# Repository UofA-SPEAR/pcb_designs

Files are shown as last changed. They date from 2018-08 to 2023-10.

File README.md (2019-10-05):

# SPEAR PCB Designs #

Central repository to hold PCB designs for SPEAR.

All board documentation shall be held in the [Wiki.](https://github.com/UofA-SPEAR/pcb_designs/wiki/).

## Onboarding

If you plan on contributing to the PCB designs, first, you need to go through this list:

1. Sign up for github, and fill out the new member form (contact the current team lead for this).
2. Follow the [GitHub Guides](https://guides.github.com/), specifically:
  - "Hello World"
  - "Understanding the GitHub flow."
  - "Documenting your projects on GitHub"
3. Follow the [Onboarding Task](https://github.com/UofA-SPEAR/pcb_designs/wiki/Onboarding-Task).

## Contributing

In order to start a new project, there are a few steps.

1. Create a new branch for your project.
2. Create a folder for your project, with the name of your project.
3. Create an Eagle library for your project.
4. Begin a documentation page on the wiki.

### Branches

Branches are a useful concept in Git, where you can work on your portion
of the project seperately from everyone else, and then "merge" your changes back in.

We make use of branches extensively. For every project, or new task, make a new branch, with
the naming scheme `project-name-yourname`, where "yourname" is ideally your first name, or at least
something that uniquely identifies you.

When you are finished your design, make a pull request to master, and assign the team
lead to review it. This is where the team lead will do a design review and ask to make
any required changes. Once these changes are made (or there are no changes), this code will be pulled into
the main repository, and the branch will be deleted.

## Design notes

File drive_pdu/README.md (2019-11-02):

# Drive System PDU #

## Overview ##

This is going to be a collaborative project, used as an EAGLE tutorial.

Features it needs to have:
- 4 Pairs of Anderson PP45 connectors
- 2 high power connectors for motor drivers
- 3v3 500mA + AMPMODU connectors for indicator board.
- Fuses

## Parts selection ##

- PP45 Parts:
	- Mouser #879-1345
	- Mouser #879-1345G6
	- Mouser #879-1336G1
- High power headers
	- TBD
- 3v3 regulator
	- TBD
- AMPMODU MTE connectors
	- DigiKey #A33893-ND
- Fuses/fuseholders
	- DigiKey #F5028-ND
	- DigiKey #486-3045-ND

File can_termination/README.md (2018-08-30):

# CAN Termination Board #

This is just a small board, designed to go on every electrical 'box' that has some options for CAN passthrough and termination to allow for a more "plug-and-play" approach to CAN bus.

It simply has two pass-through connections (so you can keep internal wiring consistent) and two termination connections (so you can hook boxes up in isolation without really worrying about which boards have termination resistors.

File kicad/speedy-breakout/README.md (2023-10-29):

# Speedy Breakout
This is a basic breakout board for our Speedy Microcontroller.
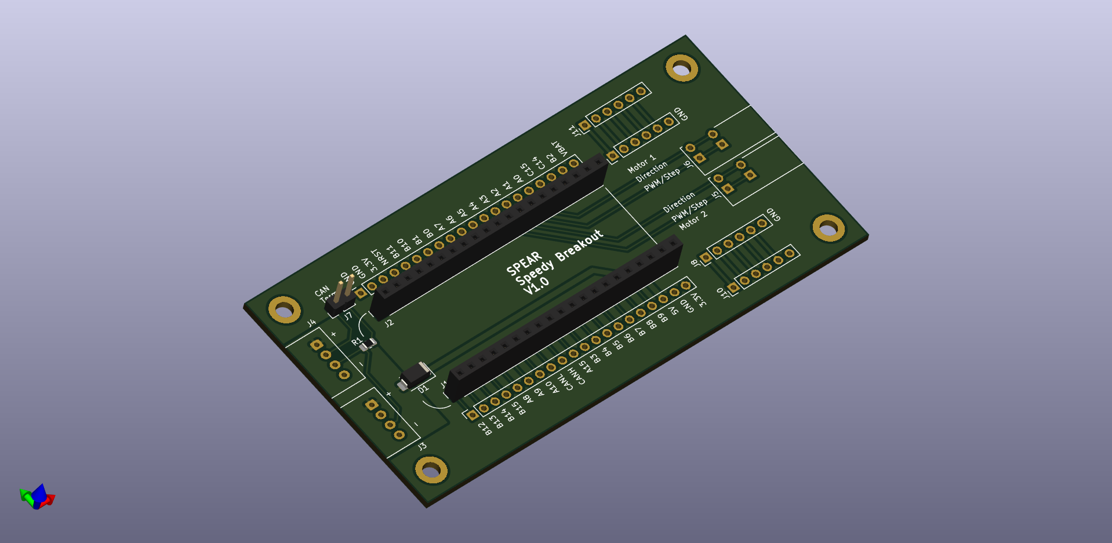
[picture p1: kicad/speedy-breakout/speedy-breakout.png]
Speedy Breakout Board 3D Model


Dimensions: 100 mm x 50 mm

## Features
- Passes 5V power from CAN bus to Speedy
- CAN connectors (Molex Mini-Lock)
- Optional CAN termination, enabled with a jumper
- Dedicated connectors to connect to motor drivers (Step/Direction or PWM/Direction)
- Through holes for all Speedy pins to ease post manufacture additions
- Through holes for adding 2.54 mm compatible headers for things like encoders

## Changelog
### V1.0: Initial design
#### Notes
- Pins A0-A3, used for the motor driver outputs, would typically be mapped to
  the 32-bit Timer 2 in the STM32, which we normally have used for the ChibiOS
  system timer. ChibiOS can use 16-bit timers so this can be worked around.
- Pins A2 and A3 on the Speedy are connected to the ST-Link chip for UART to
  USB functionality, and it seems like the ST-Link was pulling them high,
  interfering with motor driver operation. The UART functionality is provided
  by the [Black Magic Probe](https://black-magic.org/index.html) firmware. This
  can be worked around by reflashing the ST-Link MCU with official ST-Link
  firmware, which doesn't have the UART functionality.
- The CUI TBL009-254 screwless terminal blocks used for the motor driver
  outputs are a too small for stranded 22 AWG wire with wire ferrules.

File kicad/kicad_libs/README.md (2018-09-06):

# KiCAD Libraries #

This is just the folder to store all kicad components and footprints created by members of SPEAR.

Footprints and components (and by extensions, boards), should not be pushed to master unless they have been verified as correct.
I.e. the board they were used on worked.

## logos.pretty ##

This library just stores different sized logos (spear and otherwise that we would want to use)

To generate: use bitmap2component on a JPEG (PNGs don't seem to work), set transparency properly (40 seems to work for me).
Then set your DPI properly. Formula is DPI = pixels per side / measurement (inches).
Then export as: name_logo_widthxheightmm.kicad_mod

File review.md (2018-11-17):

## First Review ##

Git commit:  arm-controller-minh_review1

### Notes:

- Noticed the LF and HF crystals added. These aren't necessary.
Unless you have specific experience adding these before, take them out.

- Naming for voltage rails could do with improvement.
Ideally add + before positive voltage rails e.g. "+5V",
and VCCCAN would ideally be named +VCAN to reduce possibility of issues.

- Board size may need to be changed. I will deal with that though if it is an issue.

### Issues:

- Voltage drop of diode from CAN bus 5V.
Specification says 4.5V-5.5V, if we drop 0.7V across the diode that may
drive the voltage for the regulators too low.
Yes it is a safety thing but the diode isn't necessary.
All boards have to follow the correct standard, and will be tested with known good connections, so this is not necessary.

- Quadrature encoder inputs need to be added. Using AMPMODU MTE connectors.

- The schematic isn't the easiest to parse. The function of several components is not immediately obvious. Signals do not always follow a logical direction.

- More silkscreen text would be very useful. Which input connectors are positive? Which direction does each direction LED represent? The board needs to be directly useful without having to look at the schematic or layout files.

- Space out CAN connectors more. They are too close to solder at the moment.

### Necessary Changes:

- Add Silkscreen text to the top of the board, such as connector information.
- Remove diode from CAN bus 5V input
- Add quadrature encoder inputs
- Space out CAN connectors

### Recommended Changes:

- Add boxes and informational text to schematic for additional information
- Re-position layout to follow best practices for signal flow.
- Rename voltage rails.

### Summary

Great design. Nice clean layout.
There's a few things to change that probably should have been specified.
Also a few little issues, but it's a solid design all around.
Not the most BOM-efficient design, considering our requirements,
some portions could be removed but it's not an issue.

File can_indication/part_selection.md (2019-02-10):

# LEDS

Cree partno:    CLV1L-FKB
DigiKey partno: CLV1L-FKB-CHMMQEHBB7673673CT-ND

### Forward Voltages @ Recommmended Currents ###

Red:   @ 20mA, Vf = 2V
Green: @ 15mA, Vf = 3v1
Blue:  @ 15mA, Vf = 3v1

Resistor Selection:
Formula used: R = (3.3V - Vf) / i
Also choosing actual resistors based on common 5% decade values.
Red:   65R -> 66R
Green: 10R -> 10R
Blue:  10R -> 10R

We can change these values later, we'll just start with these.
(They'll probably be too bright)

# Micro

STM32F103CB (for now, we'll see about memory requirements.
With MCP2562 as CAN transceiver.

As well, there will be two PCA9685s to drive the LEDs.

Power should probably come from the batteries. 50mA / LED * 8 LEDs = 400mA,
which is almost half of the current we can pull from the UAVCAN micro standard.

# Connectors

JST GH 4-pin SMD connectors.
Screw terminals for power???

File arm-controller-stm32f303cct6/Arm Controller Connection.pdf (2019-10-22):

### Arm Controller Connection:

For Motor Driver 1:

INB: PA9

INA: PA10

PWM: PC8 (TIM3_CH3 or TIM8_CH3)

ENA: PC7

ENB: PC6

Current Sense: PC2 (ADC12_IN8)

For Motor Driver 2:

INB: PC9

INA: PA8

PWM: PB15 (TIM15_CH1)

ENA: PB14

ENB: PB13

Current Sense: PC3 (ADC12_IN9)

### For 2x Connector DUPONT(Pin 1 is indicated by square hole)

J4:

Pin 1: Slave Select Pin/PC12

Pin 2: General Pins, can be selected by bridging jumper:

SCK/PB3

PB5 (TIM3_CH2)

Pin 3: General Pins, can be selected by bridging jumper:

PB9 (TIM17_CH1 or TIM4_CH4)

MISO/PB4

PA6 (ADC2_IN3)

Pin 4: Power Selection (either 5V or 3V3)

Pin 5: GND

J5:

Pin 1: Slave Select Pin/PC11

Pin 2: General Pins, can be selected by bridging jumper:

SCK/PB3

PB6 (TIM4_CH1)

Pin 3: General Pins, can be selected by bridging jumper:

PB8 (TIM16_CH1 or TIM4_CH3)

MISO/PB4

PA7 (ADC2_IN4)

Pin 4: Power Selection (either 5V or 3V3)

Pin 5: GND

### ID Selection:

NODE 1: PB1

NODE 2: PB2

NODE 3: PB10

NODE 4: PB11

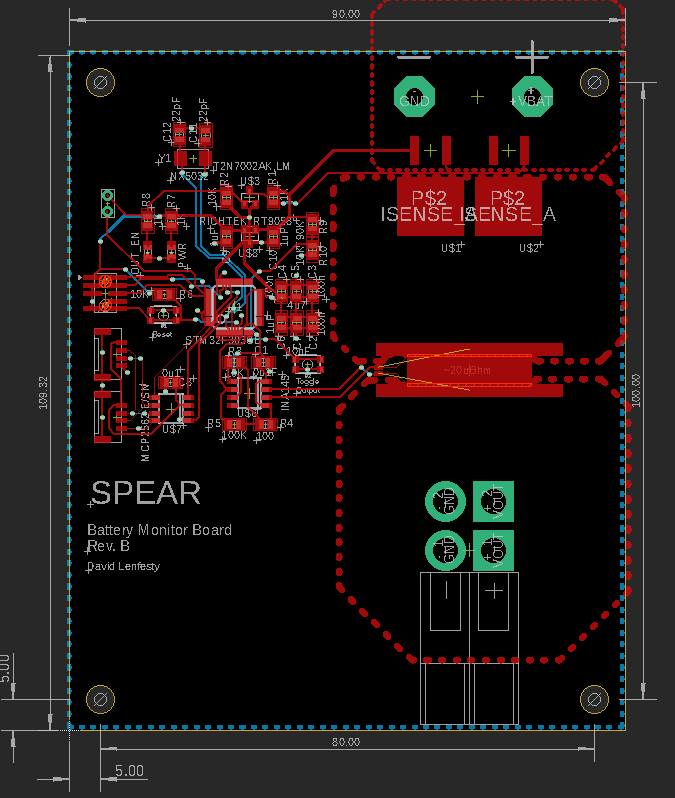
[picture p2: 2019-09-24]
battery_monitor/images/battery_monitor_r3_layout.png

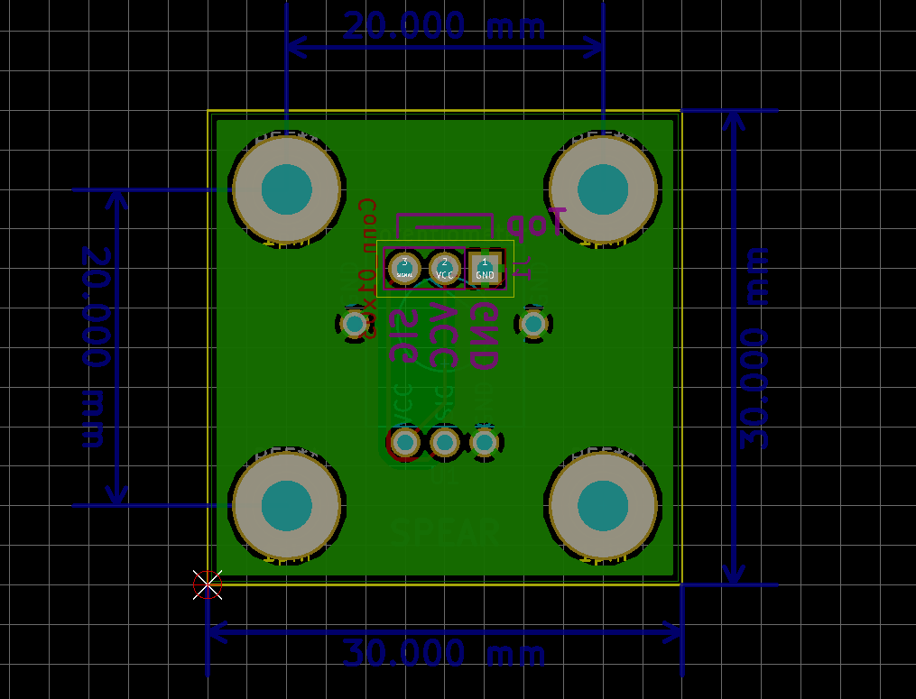
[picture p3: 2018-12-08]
kicad/position_feedback/dimensions.PNG

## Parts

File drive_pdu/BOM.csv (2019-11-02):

Part | Manufacturer | Distributer | Part Number | Distributer # | Unit Cost | Number | Total | Notes
FUSE CLIP CARTRIDGE 250V 30A PCB | Littelfuse Inc. | Digikey | 01220090Z | F4190-ND | 0.71 | 16 | 11.36
FUSE GLASS 30A 32VAC 3AB 3AG | Eaton - Electronics Division | Digikey | BK/AGC-30-R | 283-2633-ND | 0.68 | 8 | 5.44
DC DC CONVERTER 3.3V 2W | Recom Power | Digikey | R-78E3.3-0.5 | 945-1661-5-ND | 3.82 | 1 | 3.82
CONN HEADER VERT 2POS PCB TIN | TE Connectivity AMP Connectors | Digikey | 5-103669-1 | A33893-ND | 1.12 | 1 | 1.12
Heavy Duty Power Connectors PP15/45 HOUSING ONLY RED - BULK | Anderson Power Products | Mouser | 1327-BK | 879-1327-BK | 0.47 | 10 | 4.7
Heavy Duty Power Connectors PP15/45 HOUSING ONLY BLACK - BULK | Anderson Power Products | Mouser | 1327G6-BK | 879-1327G6-BK | 0.72 | 10 | 7.2
Heavy Duty Power Connectors PCB45 HORIZMNT(BOT) RALPCONTACT | Anderson Power Products | Mouser | 3-5912P1 | 879-3-5912P1 | 1.08 | 14 | 15.12
Heavy Duty Power Connectors PCB45 HORIZMNT(P) RALPCONTACT | Anderson Power Products | Mouser | 3-5912P1 | 879-3-5913P1 | 1.08 | 6 | 6.48
 |  |  |  |  |  | Total | 55.24

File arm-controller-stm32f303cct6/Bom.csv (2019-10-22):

Manufacturer Part Number | Manufacturer | Digi-Key Part Number | Customer Reference | Reference Designator | Packaging | Part Status | Quantity | Unit Price | Extended Price | Quantity Available | Mfg Std Lead Time | Description | RoHS Status | Lead Free Status | REACH Status | US Tariff Status
MCP2562T-E/SN | Microchip Technology | MCP2562T-E/SNCT-ND | ARM_CONTROL |  | Cut Tape (CT) | Active | 1 | 1.46 | $1.46 | 27560 | 14 Weeks | IC TXRX CAN 8SOIC | RoHS Compliant | Lead free | REACH Unaffected
RT6200GE | Richtek USA Inc. | RT6200GECT-ND | ARM_CONTROL |  | Cut Tape (CT) | Active | 1 | 3.32 | $3.32 | 2975 | 16 Weeks | IC REG BUCK ADJ 0.6A SOT23-6 | RoHS Compliant | Lead free | REACH Unaffected
AP2112K-3.3TRG1 | Diodes Incorporated | AP2112K-3.3TRG1DICT-ND | ARM_CONTROL |  | Cut Tape (CT) | Active | 2 | 0.75 | $1.50 | 151941 | 24 Weeks | IC REG LINEAR 3.3V 600MA SOT25 | RoHS Compliant | Lead free | REACH Unaffected | Tariff Applied
VNH5019ATR-E | STMicroelectronics | 497-13073-1-ND | ARM_CONTROL |  | Cut Tape (CT) | Active | 1 | 13 | $13.00 | 10 | Not Available | IC MTR DRV 5.5-24V MULTIPWRSO-30 | RoHS Compliant | Lead free | Not Available
SM04B-GHS-TB(LF)(SN)- | JST Sales America Inc. | 455-1566-1-ND | ARM_CONTROL |  | Cut Tape (CT) | Active | 2 | 0.66 | $1.32 | 73785 | 24 Weeks | CONN HEADER SMD R/A 4POS 1.25MM | RoHS Compliant | Lead free | Not Available
RC0805JR-071KL | Yageo | 311-1.0KARCT-ND | ARM_CONTROL |  | Cut Tape (CT) | Active | 10 | 0.056 | $0.56 | 7880762 | 16 Weeks | RES SMD 1K OHM 5% 1/8W 0805 | RoHS Compliant | Lead free | REACH Unaffected | Tariff Applied
CL21F104ZBCNNNC | Samsung Electro-Mechanics | 1276-1007-1-ND | ARM_CONTROL |  | Cut Tape (CT) | Active | 2 | 0.15 | $0.30 | 1074630 | Not Available | CAP CER 0.1UF 50V Y5V 0805 | RoHS Compliant | Lead free | REACH Unaffected
RC0805JR-074K7L | Yageo | 311-4.7KARCT-ND | ARM_CONTROL |  | Cut Tape (CT) | Active | 2 | 0.16 | $0.32 | 4683044 | 16 Weeks | RES SMD 4.7K OHM 5% 1/8W 0805 | RoHS Compliant | Lead free | REACH Unaffected | Tariff Applied
RC0805JR-071KL | Yageo | 311-1.0KARCT-ND | ARM_CONTROL |  | Cut Tape (CT) | Active | 10 | 0.056 | $0.56 | 7880762 | 16 Weeks | RES SMD 1K OHM 5% 1/8W 0805 | RoHS Compliant | Lead free | REACH Unaffected | Tariff Applied
NX5032GA-8.000M-STD-CSU-1 | NDK America, Inc. | 644-1132-1-ND | ARM_CONTROL |  | Cut Tape (CT) | Active | 1 | 1.02 | $1.02 | 199770 | 12 Weeks | CRYSTAL 8.0000MHZ 8PF SMD | RoHS Compliant | Lead free | Not Available | Tariff Applied
885012007012 | Wurth Electronics Inc. | 732-7816-1-ND | ARM_CONTROL |  | Cut Tape (CT) | Active | 2 | 0.15 | $0.30 | 4459 | 37 Weeks | CAP CER 22PF 16V C0G/NP0 0805 | RoHS Compliant | Lead free | REACH Unaffected
LTST-C171GKT | Lite-On Inc. | 160-1423-1-ND | ARM_CONTROL |  | Cut Tape (CT) | Active | 2 | 0.43 | $0.86 | 473393 | 12 Weeks | LED GREEN CLEAR CHIP SMD | RoHS Compliant | Lead free | Not Available | Tariff Applied
RR1220P-103-D | Susumu | RR12P10.0KDCT-ND | ARM_CONTROL |  | Cut Tape (CT) | Active | 1 | 0.17 | $0.17 | 921061 | 16 Weeks | RES SMD 10K OHM 0.5% 1/10W 0805 | RoHS Compliant | Lead free | Not Available | Tariff Applied
IPB80N03S4L03ATMA1 | Infineon Technologies | IPB80N03S4L03ATMA1CT-ND | ARM_CONTROL |  | Cut Tape (CT) | Active | 1 | 2.57 | $2.57 | 780 | Not Available | MOSFET N-CH 30V 80A TO263-3 | RoHS Compliant | Lead free | Not Available
CL21A106KQCLRNC | Samsung Electro-Mechanics | 1276-2405-1-ND | ARM_CONTROL |  | Cut Tape (CT) | Active | 1 | 0.16 | $0.16 | 51390 | Not Available | CAP CER 10UF 6.3V X5R 0805 | RoHS Compliant | Lead free | REACH Unaffected | Tariff Applied
TPSE107M025R0150 | AVX Corporation | 478-10758-1-ND | ARM_CONTROL |  | Cut Tape (CT) | Active | 1 | 4.66 | $4.66 | 4944 | 15 Weeks | CAP TANT 100UF 20% 25V 2917 | RoHS Compliant | Lead free | REACH Unaffected
CL21A475KLCLQNC | Samsung Electro-Mechanics | 1276-6722-1-ND | ARM_CONTROL |  | Cut Tape (CT) | Active | 1 | 0.35 | $0.35 | 1213767 | Not Available | CAP CER 4.7UF 35V X5R 0805 | RoHS Compliant | Lead free | REACH Unaffected | Tariff Applied
219-4LPSTR | CTS Electrocomponents | CT3116CT-ND | ARM_CONTROL |  | Cut Tape (CT) | Active | 1 | 1.34 | $1.34 | 10433 | 8 Weeks | SWITCH SLIDE DIP SPST 100MA 20V | RoHS Compliant | Lead free | Not Available
ERA-6AEB913V | Panasonic Electronic Components | P91KDACT-ND | ARM_CONTROL |  | Cut Tape (CT) | Active | 1 | 0.56 | $0.56 | 15398 | 22 Weeks | RES SMD 91K OHM 0.1% 1/8W 0805 | RoHS Compliant | Lead free | REACH Unaffected
RC0805FR-0717K4L | Yageo | 311-17.4KCRCT-ND | ARM_CONTROL |  | Cut Tape (CT) | Active | 1 | 0.16 | $0.16 | 388172 | 16 Weeks | RES SMD 17.4K OHM 1% 1/8W 0805 | RoHS Compliant | Lead free | REACH Unaffected | Tariff Applied
1935161 | Phoenix Contact | 277-1667-ND | ARM_CONTROL |  | Bulk | Active | 2 | 0.63 | $1.26 | 100614 | 15 Weeks | TERM BLK 2POS SIDE ENTRY 5MM PCB | RoHS Compliant | Lead free | Not Available
5-103669-3 | TE Connectivity AMP Connectors | A33897-ND | ARM_CONTROL |  | Tube | Active | 1 | 1.34 | $1.34 | 3111 | 4 Weeks | CONN HEADER VERT 4POS 2.54MM | RoHS Compliant | Lead free | Not Available
ERA-6AEB202V | Panasonic Electronic Components | P2.0KDACT-ND | ARM_CONTROL |  | Cut Tape (CT) | Active | 2 | 0.56 | $1.12 | 145048 | 22 Weeks | RES SMD 2K OHM 0.1% 1/8W 0805 | RoHS Compliant | Lead free | REACH Unaffected
ERA-6AEB332V | Panasonic Electronic Components | P3.3KDACT-ND | ARM_CONTROL |  | Cut Tape (CT) | Active | 1 | 0.56 | $0.56 | 139080 | 22 Weeks | RES SMD 3.3K OHM 0.1% 1/8W 0805 | RoHS Compliant | Lead free | REACH Unaffected
74404032150 | Wurth Electronics Inc. | 732-5498-1-ND | ARM_CONTROL |  | Cut Tape (CT) | Active | 1 | 1.71 | $1.71 | 4728 | 13 Weeks | FIXED IND 15UH 730MA 300 MOHM | RoHS Compliant | Lead free | REACH Unaffected | Tariff Eligible
742792651 | Wurth Electronics Inc. | 732-1593-1-ND | ARM_CONTROL |  | Cut Tape (CT) | Active | 1 | 0.25 | $0.25 | 300952 | 12 Weeks | FERRITE BEAD 600 OHM 0603 1LN | RoHS Compliant | Lead free | REACH Unaffected
CL21B333KBANNNC | Samsung Electro-Mechanics | 1276-1796-1-ND | ARM_CONTROL |  | Cut Tape (CT) | Active | 1 | 0.16 | $0.16 | 391390 | Not Available | CAP CER 0.033UF 50V X7R 0805 | RoHS Compliant | Lead free | REACH Unaffected

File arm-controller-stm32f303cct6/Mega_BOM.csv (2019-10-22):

Index | Quantity | Part Number | Manufacturer Part Number | Description | Customer Reference | Available | Backorder | Unit Price | Extended Price CAD
1 | 3 | 493-2226-1-ND | UWT1H101MNL1GS | CAP ALUM 100UF 20% 50V SMD | ARM_CONTROL | 3 | 0 | 0.71000 | 2.13
2 | 1 | MCP2562T-E/SNCT-ND | MCP2562T-E/SN | IC TXRX CAN 8SOIC | ARM_CONTROL | 1 | 0 | 1.40000 | 1.40
3 | 2 | AP2112K-3.3TRG1DICT-ND | AP2112K-3.3TRG1 | IC REG LINEAR 3.3V 600MA SOT25 | ARM_CONTROL | 2 | 0 | 0.72000 | 1.44
4 | 2 | 497-13073-1-ND | VNH5019ATR-E | IC MTR DRV 5.5-24V MULTIPWRSO-30 | ARM_CONTROL | 2 | 0 | 12.50000 | 25.00
5 | 2 | 455-1566-1-ND | SM04B-GHS-TB(LF)(SN)- | CONN HEADER SMD R/A 4POS 1.25MM | ARM_CONTROL | 2 | 0 | 0.64000 | 1.28
6 | 6 | 1276-1007-1-ND | CL21F104ZBCNNNC | CAP CER 0.1UF 50V Y5V 0805 | ARM_CONTROL | 6 | 0 | 0.14000 | 0.84
7 | 9 | 311-1.0KARCT-ND | RC0805JR-071KL | RES SMD 1K OHM 5% 1/8W 0805 | ARM_CONTROL | 9 | 0 | 0.15000 | 1.35
8 | 1 | 644-1132-1-ND | NX5032GA-8.000M-STD-CSU-1 | CRYSTAL 8.0000MHZ 8PF SMD | ARM_CONTROL | 1 | 0 | 1.04000 | 1.04
9 | 2 | 732-7816-1-ND | 885012007012 | CAP CER 22PF 16V C0G/NP0 0805 | ARM_CONTROL | 2 | 0 | 0.14000 | 0.28
10 | 1 | 160-1423-1-ND | LTST-C171GKT | LED GREEN CLEAR CHIP SMD | ARM_CONTROL | 1 | 0 | 0.40000 | 0.40
11 | 2 | 1276-2405-1-ND | CL21A106KQCLRNC | CAP CER 10UF 6.3V X5R 0805 | ARM_CONTROL | 2 | 0 | 0.18000 | 0.36
12 | 1 | CT3116CT-ND | 219-4LPSTR | SWITCH SLIDE DIP SPST 100MA 20V | ARM_CONTROL | 1 | 0 | 1.29000 | 1.29
13 | 4 | 277-1667-ND | 1935161 | TERM BLK 2POS SIDE ENTRY 5MM PCB | ARM_CONTROL | 4 | 0 | 0.61000 | 2.44
14 | 1 | 732-1593-1-ND | 742792651 | FERRITE BEAD 600 OHM 0603 1LN | ARM_CONTROL | 1 | 0 | 0.24000 | 0.24
15 | 2 | 1276-1796-1-ND | CL21B333KBANNNC | CAP CER 0.033UF 50V X7R 0805 | ARM_CONTROL | 2 | 0 | 0.14000 | 0.28
16 | 2 | A33899-ND | 5-103669-4 | CONN HEADER VERT 5POS 2.54MM | ARM_CONTROL | 2 | 0 | 1.84000 | 3.68
17 | 4 | A34194-ND | 5-103958-4 | CONN RCPT 5POS IDC 22-26AWG GOLD | ARM_CONTROL | 4 | 0 | 2.81000 | 11.24
18 | 1 | SAM9433-ND | FTSH-105-01-F-DV-007 | CONN HEADER SMD 10POS 1.27MM | ARM_CONTROL | 1 | 0 | 2.55000 | 2.55
19 | 2 | IRLR8726TRPBFCT-ND | IRLR8726TRPBF | MOSFET N-CH 30V 86A DPAK | ARM_CONTROL | 2 | 0 | 0.75000 | 1.50
20 | 1 | 497-17421-ND | STM32F303CBT6 | IC MCU 32BIT 128KB FLASH 48LQFP | ARM_CONTROL | 1 | 0 | 7.78000 | 7.78
21 | 7 | 311-10.0KCRCT-ND | RC0805FR-0710KL | RES SMD 10K OHM 1% 1/8W 0805 | ARM_CONTROL | 7 | 0 | 0.15000 | 1.05
22 | 1 | CKN10361CT-ND | RS-187R05A2-DS MT RT | SWITCH TACTILE SPST-NO 0.05A 12V | ARM_CONTROL | 1 | 0 | 0.80000 | 0.80

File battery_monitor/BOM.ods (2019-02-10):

Part | Manufacturer | Distributor | Partno. | Distributor Partno. | Unit Cost | Number | Total Cost | Notes
P-MOS Switch | Infineon | DigiKey | IPB120P04P4L03ATMA1 | IPB120P04P4L03ATMA1CT-ND | 3.94 | 2 | 7.88 | Cost could be lowered if we used N-channel
Microcontroller | STMicro | DigiKey | STM32F303CBT6 | 497-17421-ND | 7.8 | 1 | 7.8
CAN Transceiver | Microchip | DigiKey | MCP2562T-E/SN | MCP2562T-E/SNCT-ND | 1.4 | 1 | 1.4
CAN Connector | JST | DigiKey | SM04B-GHS-TB(LF)(SN)- | 455-1566-1-ND | 0.64 | 2 | 1.28
3v3 Regulator | Richtek | DigiKey | RT9058-33GV | 1028-1253-1-ND | 1.07 | 1 | 1.07
MOSFET N-CH 60V 1.6A SOT-23 | Diodes Incorporated | DigiKey | DMN6140L-7 | DMN6140L-7DICT-ND | 0.65 | 1 | 0.65
CONN HEADER SMD 10POS 1.27MM | Samtec Inc. | DigiKey | FTSH-105-01-F-DV-007 | SAM9433-ND | 2.55 | 1 | 2.55 | Programming Header
Indication LEDs |  |  |  |  | 0 | 2 | 0 | David has a bunch extra to use.
CAP CER 0.1UF 50V Y5V 0805 | Samsung Electro-Mechanics | DigiKey | CL21F104ZBCNNNC | 1276-1007-1-ND | 0.14 | 5 | 0.7
CAP CER 4.7UF 35V X5R 0805 | Samsung Electro-Mechanics | DigiKey | CL21A475KLCLQNC | 1276-6722-1-ND | 0.34 | 1 | 0.34
CAP CER 10000PF 50V X7R 0805 | Yageo | DigiKey | CC0805KRX7R9BB103 | 311-1136-1-ND | 0.2 | 1 | 0.2
CAP CER 1UF 50V Y5V 0805 | Samsung Electro-Mechanics | DigiKey | CL21F105ZBFNNNE | 1276-3010-1-ND | 0.21 | 1 | 0.21
CAP CER 22PF 50V C0G/NPO 0805 | Yageo | DigiKey | CC0805JRNPO9BN220 | 311-1103-1-ND | 0.2 | 2 | 0.4
RES SMD 100K OHM 1% 1/8W 0805 | Yageo | DigiKey | RC0805FR-07100KL | 311-100KCRCT-ND | 0.15 | 1 | 0.15
RES SMD 10K OHM 0.5% 1/10W 0805 | Susumu | DigiKey | RR1220P-103-D | RR12P10.0KDCT-ND | 0.17 | 4 | 0.68
RES SMD 1K OHM 0.5% 1/10W 0805 | Susumu | DigiKey | RR1220P-102-D | RR12P1.0KDCT-ND | 0.17 | 3 | 0.51
RES SMD 100 OHM 1% 1/8W 0805 | Yageo | DigiKey | RC0805FR-07100RL | 311-100CRCT-ND | 0.15 | 1 | 0.15
Red PP45 Housing | Anderson PP | Mouser | 1327-BK | 879-1327-BK | 0.47 | 2 | 0.94 | When trying to find on mouser, specify “-” for current.
Black PP45 Housing | Anderson PP | Mouser | 1327G6-BK | 879-1327G6-BK | 0.72 | 2 | 1.44
Bottom row PP45 Connector | Anderson PP | Mouser | 3-5912P1 | 879-3-5912P1 | 1.08 | 2 | 2.16
Top row PP45 Connector | Anderson PP | Mouser | 3-5913P1 | 879-3-5913P1 | 1.3 | 2 | 2.6
RES SMD 91K OHM 1% 1/8W 0805 | Yageo | DigiKey | RC0805FR-0791KL | 311-91.0KCRCT-ND | 0.15 | 1 | 0.15
CRYSTAL 8.0000MHZ 8PF SMD | NDK America, Inc. | DigiKey | NX5032GA-8.000M-STD-CSU-1 | 644-1132-1-ND | 0.98 | 1 | 0.98
 |  |  |  |  |  | Total Cost | 33.11

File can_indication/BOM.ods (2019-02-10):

Part | Manufacturer | Distributor | Manufacturer Partno. | Distributer Partno. | Unit Cost | Quantity | Total Cost | Notes
IC TXRX CAN 8SOIC | Microchip Technology | DigiKey | MCP2562T-E/SN | MCP2562T-E/SNCT-ND | 1.42 | 1 | 1.42
IC MCU 32BIT 128KB FLASH 48LQFP | STMicroelectronics | DigiKey | STM32F303CBT6 | 497-17421-ND | 7.9 | 1 | 7.9
CONN HEADER VERT 2POS PCB TIN | TE Connectivity AMP Connectors | DigiKey | TE Connectivity AMP Connectors | A33893-ND | 1.13 | 1 | 1.13
CAP CER 0.1UF 50V Y5V 0805 | Samsung Electro-Mechanics | DigiKey | CL21F104ZBCNNNC | 1276-1007-1-ND | 0.14 | 4 | 0.56
CAP CER 4.7UF 35V X5R 0805 | Samsung Electro-Mechanics | DigiKey | CL21A475KLCLQNC | 1276-6722-1-ND | 0.34 | 1 | 0.34
RES SMD 10K OHM 0.5% 1/10W 0805 | Susumu | DigiKey | RR1220P-103-D | RR12P10.0KDCT-ND | 0.17 | 4 | 0.68
LED RGB DIFFUSED 4PLCC SMD | Cree Inc. | DigiKey | CLV1L-FKB-CHMMQEHBB7673673 | CLV1L-FKB-CHMMQEHBB7673673CT-ND | 0.5 | 8 | 4
RES SMD 1K OHM 0.5% 1/10W 0805 | Susumu | DigiKey | RR1220P-102-D | RR12P1.0KDCT-ND | 0.15 | 24 | 3.6
IC LED DRIVER RGBA 28-TSSOP | NXP USA Inc. | DigiKey | PCA9685PW,118 | 568-11925-1-ND | 3.56 | 2 | 7.12
CONN HEADER GH SIDE 4POS 1.25MM | JST Sales America Inc. | DigiKey | SM04B-GHS-TB(LF)(SN)- | 455-1566-1-ND | 0.65 | 2 | 1.3
 |  |  |  |  |  | Total: | 28.05

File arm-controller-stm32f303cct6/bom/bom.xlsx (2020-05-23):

Comment | Designator | Footprint | LCSC Part #（optional）
1uF | C1,C2,C3 | 0805_C
100nF | C4, C8, C11 | 0805_C
330uF | C6, C7 | 1010-US140-CPOL
10kOhm | R1,R2,R6 | 0805_R
0.005Ohm | R3 | WSC4527
33kOhm | R4 | 0805_R
7.5kOhm | R5 | 0805_R
STL90N6F7 | U$1,U$2,U$3 | DFN8-5x6
SCREW-TERM 5MM | J1,J2 | Screw-term-5mm
NC7SZ157P6 | IC1 | SOT65-6
TS5A3357DCUT | IC2 | SOP50-8N
TE 5-103669-4 | J3 | DUPONT5
0534260510-MOLEX | JP1,JP2 | Molex connector

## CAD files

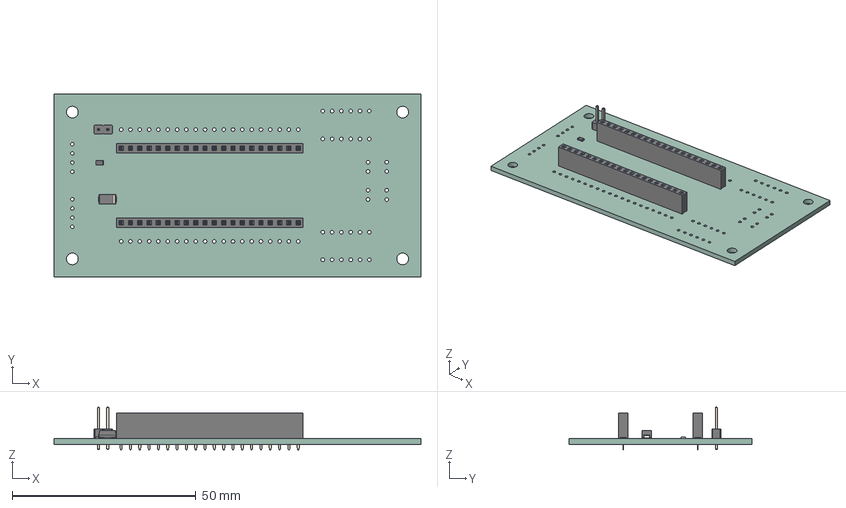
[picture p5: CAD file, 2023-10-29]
kicad/speedy-breakout/speedy-breakout.step
100.0 x 50.0 x 11.6 mm
speedy-breakout PCB

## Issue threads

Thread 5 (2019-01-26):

Raspberry Pi CAN hat header position.

davidlenfesty, 2019-01-26:
It's upside down.

davidlenfesty, 2019-01-30:
Fixed with commit 5ae3708d0cc06c5adba2eaca92888ab961b0cd47

Closed 2019-01-30.

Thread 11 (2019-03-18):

Computer PDU

davidlenfesty, 2019-03-18:
# Computer Power Distribution Board

Not a full review yet, I have not had a large amount of time to go over.

## Schematic

Nice and clean.

- [x] Labels/net names for some of the more important nets would be nice.
- [x] CAN bus lines NEED to be hooked together.

TODO (for me, the reviewer):
- [x] Verify converter design
- [x] Check availability/cost/etc. on digikey

## Layout

Again, nice and clean. Has a few DRC errors that need to be fixed though.

- [x] Not necessary, but a bottom-side groundplane should be added.
- [x] Power traces need to be made wider/polygons
- [x] I'm not entirely sure what the layout guidelines are for the converters, not really sure what is good/bad for power supply design. May want to look in a little more detail into those.

Closed 2019-04-13.

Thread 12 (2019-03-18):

Arm Controller Rev. B (Mega)

davidlenfesty, 2019-03-18:
# Arm Controller Rev. B

I appreciate the naming :grin:.

Still more stuff to review, this is just first impressions and most of the issues I've noticed.

## Schematic

Looks nice. Obviously the first board worked, so no major changes is good. Nice attention to detail on the jumpers for the encoder inputs.
- [ ] Some bounding boxes would be nice, just to visually seperate the different parts.

TODO (for me):
- [ ] verify the pinouts

## Layout

Nice and pretty. I especially like the rounded edges and the improvements in the soldermask.
- [ ] We do have more board space on this one, so even though we haven't had issues with overheating, it would be nice if we could shift things around to increase copper surface area with the power traces.
- [ ] The bottom right screw hole is inside the copper pour of a power trace. The trace should be moved away or at least expand the keepaway zone for the copper pour.

davidlenfesty, 2020-02-03:
Pre-Beefy!

Closed 2020-02-03.

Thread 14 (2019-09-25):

RC Input Board

davidlenfesty, 2019-09-25:
Needs new connectors.

davidlenfesty, 2019-10-26:
We are switching from JST GH connectors, as they are small and very finicky to make cables for.

The new connector we are using is the [Molex Mini-Lock series](http://www.literature.molex.com/SQLImages/kelmscott/Molex/PDF_Images/987651-9241.PDF).

Here is the [engineering drawing](https://www.molex.com/pdm_docs/sd/534260410_sd.pdf).

Specifically, we need the 4-pin version. We will follow the UAVCAN [micro connector standard](https://uavcan.org/Specification/8._Hardware_design_recommendations/#uavcan-micro-connector), with pin 1 (circuit 1) as 5V, 2 as CANH, 3 as CANL, and 4 as GND.

Closed 2022-05-14.

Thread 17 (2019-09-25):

Redesign Battery Monitoring Board

davidlenfesty, 2019-09-25:
Has issues with transient effects on battery plug/unplug. Among others.

See [wiki page](https://github.com/UofA-SPEAR/pcb_designs/wiki/Battery-Monitoring-Board)

davidlenfesty, 2020-02-03:
We are not going to implement these anymore (not before URC anyways), as everything else will have power monitoring anyways and fusing is necessary no matter what.

Closed 2020-02-03.

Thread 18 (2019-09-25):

Design Arm Systems PDU

davidlenfesty, 2019-09-25:
Needs to fit on new tray design

davidlenfesty, 2019-11-01:
Important part numbers (DigiKey):

- ATO-style fuse holders - WK6265-ND

davidlenfesty, 2019-11-02:
The input connectors should be consolidated into one double-stacked header. Output connectors should be changed to anderson powerpole style. Fuses should be changed to ATO style. THe 3v3 regulator should be removed.

davidlenfesty, 2020-02-03:
Output should be changed to screwless terminal blocks and 6 high current nets and 1 low current extra net.

JackOpgenorth, 2022-05-14:
This is done, but needs more testing

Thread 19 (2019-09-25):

Design Drive Systems PDU

davidlenfesty, 2019-09-25:
Needs to fit on new tray design.

davidlenfesty, 2020-02-03:
# Drive PDU Requirements
- Doubled up anderson input header
- 5 fused output rails (using automotive ATC fuses), 4 for drive controllers, 1 extra with more smaller terminals
- Uses screwless terminal headers.

JackOpgenorth, 2022-05-14:
This issue is done, but needs more testing

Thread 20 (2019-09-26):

Revise Indication Board

davidlenfesty, 2019-09-26:
This board is important now.

New competition rules say we need a bright RGB indicator board to say what autonomy modes we are in.

Chages to be made: instead of 8 low power RGB leds we need one or two higher power ones. Also the CAN connectors need to be changed, and possibly a programming header.

davidlenfesty, 2019-11-21:
To find the LED driver, go to digikey, find the IC -> PMIC LED Driver category, and search fo linear types with 3 outputs, and you will have to figure out the current needed, and find an appropriate LED as well.

JackOpgenorth, 2022-05-14:
Closing, this is no longer needed

Closed 2022-05-14.

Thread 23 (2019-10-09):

Finish Setting up Arm

davidlenfesty, 2019-10-09:
Once mechanical team has the tray system, we will need to integrate the arm fully into the rover.

Tasks:
- [ ] Make connectors, etc. to hook up sensors and motors on the arm.
- [ ] Finish fixing firmware, ensure it works with arm board rev. 2
- [ ] Hook in arm, configure arm controllers.

minh7a6, 2019-10-10:
what type of sensors are we gonna put in the arm besides encoder?

davidlenfesty, 2019-10-10:
Just the different arm encoders

Closed 2020-01-21.

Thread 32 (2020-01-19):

Motor Control Board Rev. B

davidlenfesty, 2020-01-19:
# Improvements to make

- Switch to screwless terminals
- Add a power LED
- Add a 5V protection diode
- Parallel current sense resistors
- Reverse polarity protection
- General layout improvements

davidlenfesty, 2021-08-16:
Addressed by Beefy design

Closed 2021-08-16.

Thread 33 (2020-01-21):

Prep for Arm Test

davidlenfesty, 2020-01-21:
The following tasks need to be completed before the arm test this weekend:

(not necessarily complete)

# Assembly
- [ ] Finish soldering motor controller boards
- [ ] Test all motor controller boards (minh)
- [ ] Make 5 CAN bus cables with the new connectors (4 double-ended, one to solder directly to the comms hub)
- [ ] Verify power distribution
- [ ] Wire in arm encoders
    - [ ] Re-pin linear actuator to the correct pinout
    - [ ] Re-pin shoulder yaw
    - [ ] Make connector for elbow
    - [ ] make connector/solder to the wrist pot
    - [ ] either other wrist motor or grabber, decide which one is easier
- [ ] Wire arm motors

# Design Verification
- [ ] Verify multiplexers work (minh)
- [ ] Finish porting arm control firmware (David & Evan)
- [ ] Debug motor controller firmware

Comment below with info.

Closed 2020-02-03.

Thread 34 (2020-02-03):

Computer PDU/Power Converters

davidlenfesty, 2020-02-03:
Singular PDU w/3 power converters onboard.

I would like each converter to be identical so swaps are easy, but if it's not practical it's not necessary.

# Power converter Requirements

- At least 18-24V input. Ideally 10-30V
- 5-24V/4A output (peak current is at 12V, min. at 24V is 0.5A, min at 5V is 1A)
- Current sensing
- Short circuit protection

## Nice-to-haves

- Overcurrent protection (set by microcontroller somehow)

# PDU Requirements

## Power Connections
- Anderson connector input ( 2 high would be nice, but not necessary)
- 3 pair screwless terminal blocks (spring loaded) per power rail. (3 +ve and 3 -ve connections)
- Pin header jumpers to connect CAN 5V line to any power converter

## Comms connections

- 2x Molex mini-lock connectors for CAN to speedy (and jumpered 5V)

davidlenfesty, 2020-02-03:
I would also like the converters to be swappable so we can replace one if something happens to it.

davidlenfesty, 2021-09-12:
These need to be tested, design is complete.

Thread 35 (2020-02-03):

Redesign Comms Hub

davidlenfesty, 2020-02-03:
# Comms Hub Requirements
- Molex Mini-Lock CAN connector (with the CORRECT pinout)
- Jumper to select if we want to provide CAN with 5V.
- Footprints for 2 CAN buses, we'll just only poopulate one. (if you can fit the GPS w/o the second CAN bus, the GPS is preferred.
- Put the GPS on it if it will fit.
- We can get rid of all the extra stuff on the board.

GPS will need to go to one of the UART lines on the TX2

Closed 2021-09-12.

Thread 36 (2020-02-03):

Get parts together for kill switch & battery fusing

davidlenfesty, 2020-02-03:
[Fuseholder](https://www.digikey.ca/product-detail/en/Littelfuse+Inc./01520008Z/F10741-ND/2518487)

[Example Relay](https://www.digikey.ca/product-detail/en/Omron+Electronics+Inc-EMC+Div/G9TB-U1ATH-E+DC12/Z8844-ND/8593135]

I think I want the relays mounted high side and the fuses mounted low side on the batteries.

I would like a common ground during normal operation, but it doesn't make a difference when the fuse blows, so that doesn't matter.

# Tasks:
- [ ] Find all mating parts for fuseholder
- [ ] Find actual relay
- [ ] Find supplier of small amount of large wire.
- [ ] Find killswitch with better terminals.
- [ ] Design a 3d-printed plate to mount these onto.

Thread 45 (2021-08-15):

Back-EMF protection on the Beefy

davidlenfesty, 2021-08-15:
It currently has none, besides the MOSFET's internal free-wheeling diodes, and probably could have avoided us breaking down for our dexterity task.

Note: this presents weirdly due to the input voltage protection, it doesn't appear to be a short until power is applied, and then it just blows through fuses, this should also get documented somewhere.

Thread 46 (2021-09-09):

Update subsys pdu to include relays

rpshukla, 2021-09-09:
Update the board to have relays and a method to control the relays

davidlenfesty, 2021-09-09:
I don't think we'll be using this feature. Maybe future work way down the line but as of right now we're aiming for simplicity.

Closed 2021-09-09.

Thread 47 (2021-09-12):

Subsystem PDU re-design

davidlenfesty, 2021-09-12:
The subsystem PDU is mostly functional, however it needs a few fixes before it's "production ready".

Required Improvements:
- Reverse XT60 connectors to correct their orientation.
- Add LED's to indicate input power and each output channel (ideally different colours, maybe green on input and red on output?)
- Fix thermal relief sizes on copper pour, they are currently much too small.

@GV-Singh2000 Please install EAGLE (you can get a student license with your ualberta email, although the process is a bit convoluted right now, I think you have to install Fusion 360 first? it's weird.) and add this repo to your projects search directory. If you're not sure we can organize a time to go over it together and go over the board as well.

GV-Singh2000, 2021-09-12:
OK, I will start by installing EAGLE or Fusion 360 Firs and then I guess I might need some help as I have no idea what the above things really mean, Its Embarrassing but I will try my Best to understand and work on them

davidlenfesty, 2021-09-12:
All good, we'll go over it in person then, I'll figure out when I have time this week (labs all start so it will be a bit hectic for me.

GV-Singh2000, 2021-09-12:
Sure, Thank you its same for me, I have 4 labs every week from Monday to Thursday 2-5 PM.

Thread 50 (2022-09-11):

Feasibility of new designs

JackOpgenorth, 2022-09-11:
We are considering switching over to Servo or Stepper motors for the new rover design. If we are designing new boards for this, need to figure out what materials we will need, and weather or not we are able to get them with the ongoing chip shortage

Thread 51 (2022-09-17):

Speedy pinouts on schematic don't intuitively match PCB layout

nic3-14159, 2022-09-17:
As the following images show, the pinouts on the schematic don't intuitively map to the layout of the actual PCB. The schematic shows the pin numberings increasing in parallel as you go down the headers, whereas the pin numbers on the PCB increase in opposite directions (pin 1 is marked with the square).

Flip the ordering of one of the headers on the schematic so that it more intuitively maps to the PCB, allowing for easier cross referencing by simply holding up the Speedy beside the header pinout on the schematic.

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

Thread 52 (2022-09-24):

Stepper motor controller

JackOpgenorth, 2022-09-24:
MechE hasn't confirmed anything at the moment, but there's a good chance that we will be using stepper motors for the arm. Need to look into either making or buying an off the shelf controller

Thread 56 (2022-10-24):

Comp PDU design re-evaluation

JackOpgenorth, 2022-10-24:
i.e: Does this board have everything we need for it to perform its function?

JackOpgenorth, 2022-10-30:
Stuff we should probably consider
- A proper connector for battery and not just SMD pads
- swap 12V output since we are using the pi (5V I think?)
- currently buck and boost are rated for 5A, this may need to change for pi
- currently we have screw terminals for connecting to the pi, could use USB instead. This might be unstable though, would hate for this to disconnect in the middle of competition

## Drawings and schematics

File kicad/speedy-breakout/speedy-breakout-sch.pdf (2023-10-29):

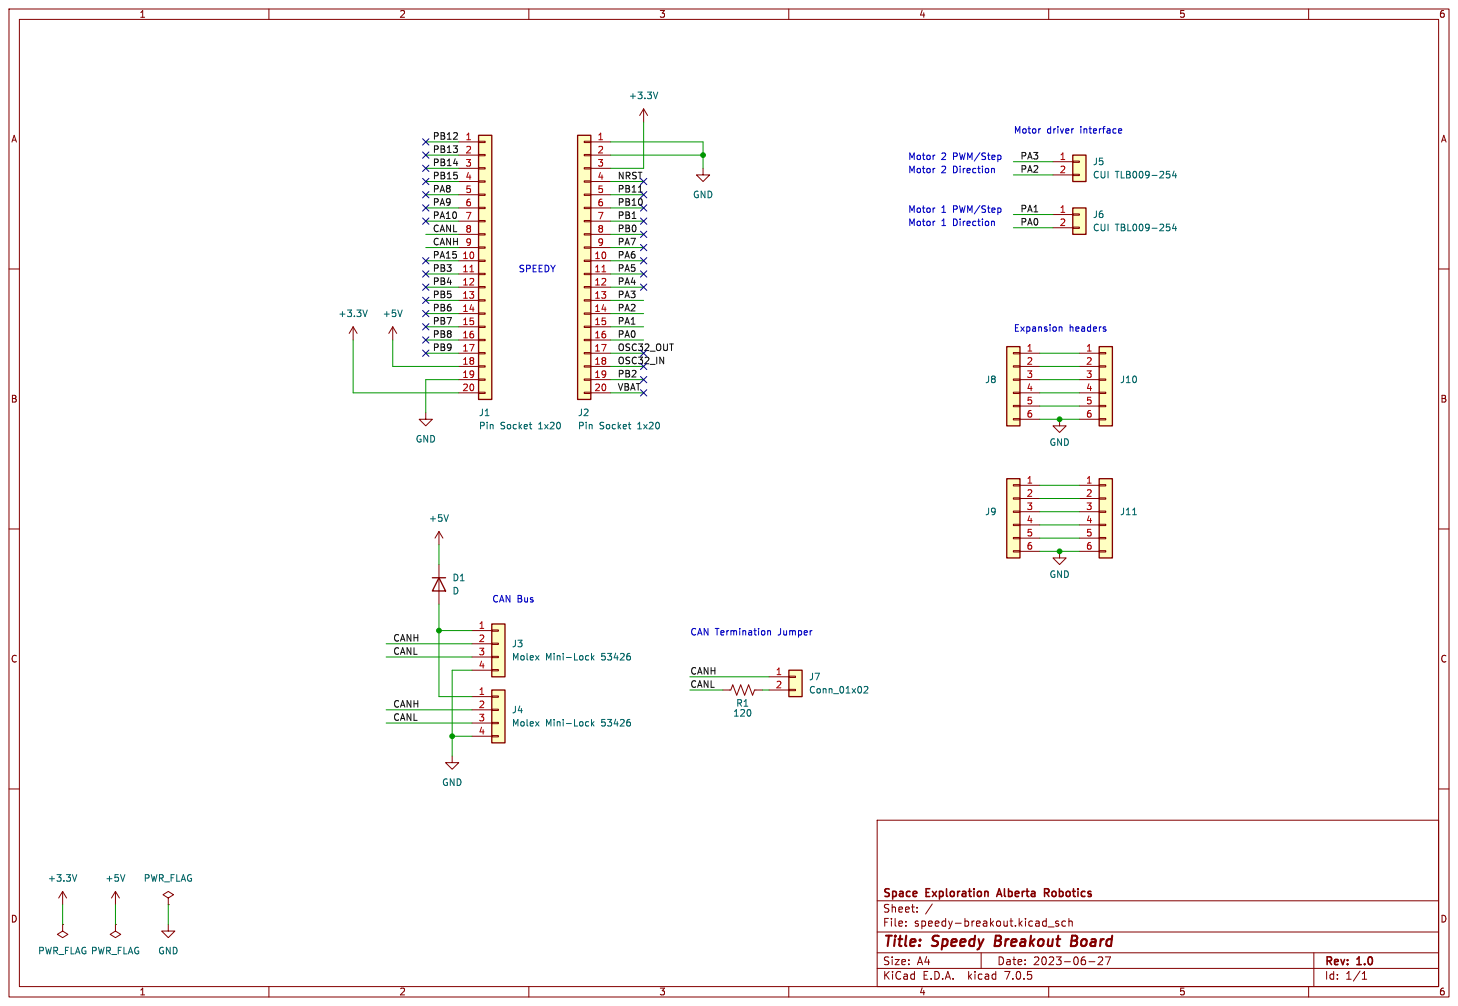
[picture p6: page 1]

Id: 1/1 Title: Speedy Breakout Board

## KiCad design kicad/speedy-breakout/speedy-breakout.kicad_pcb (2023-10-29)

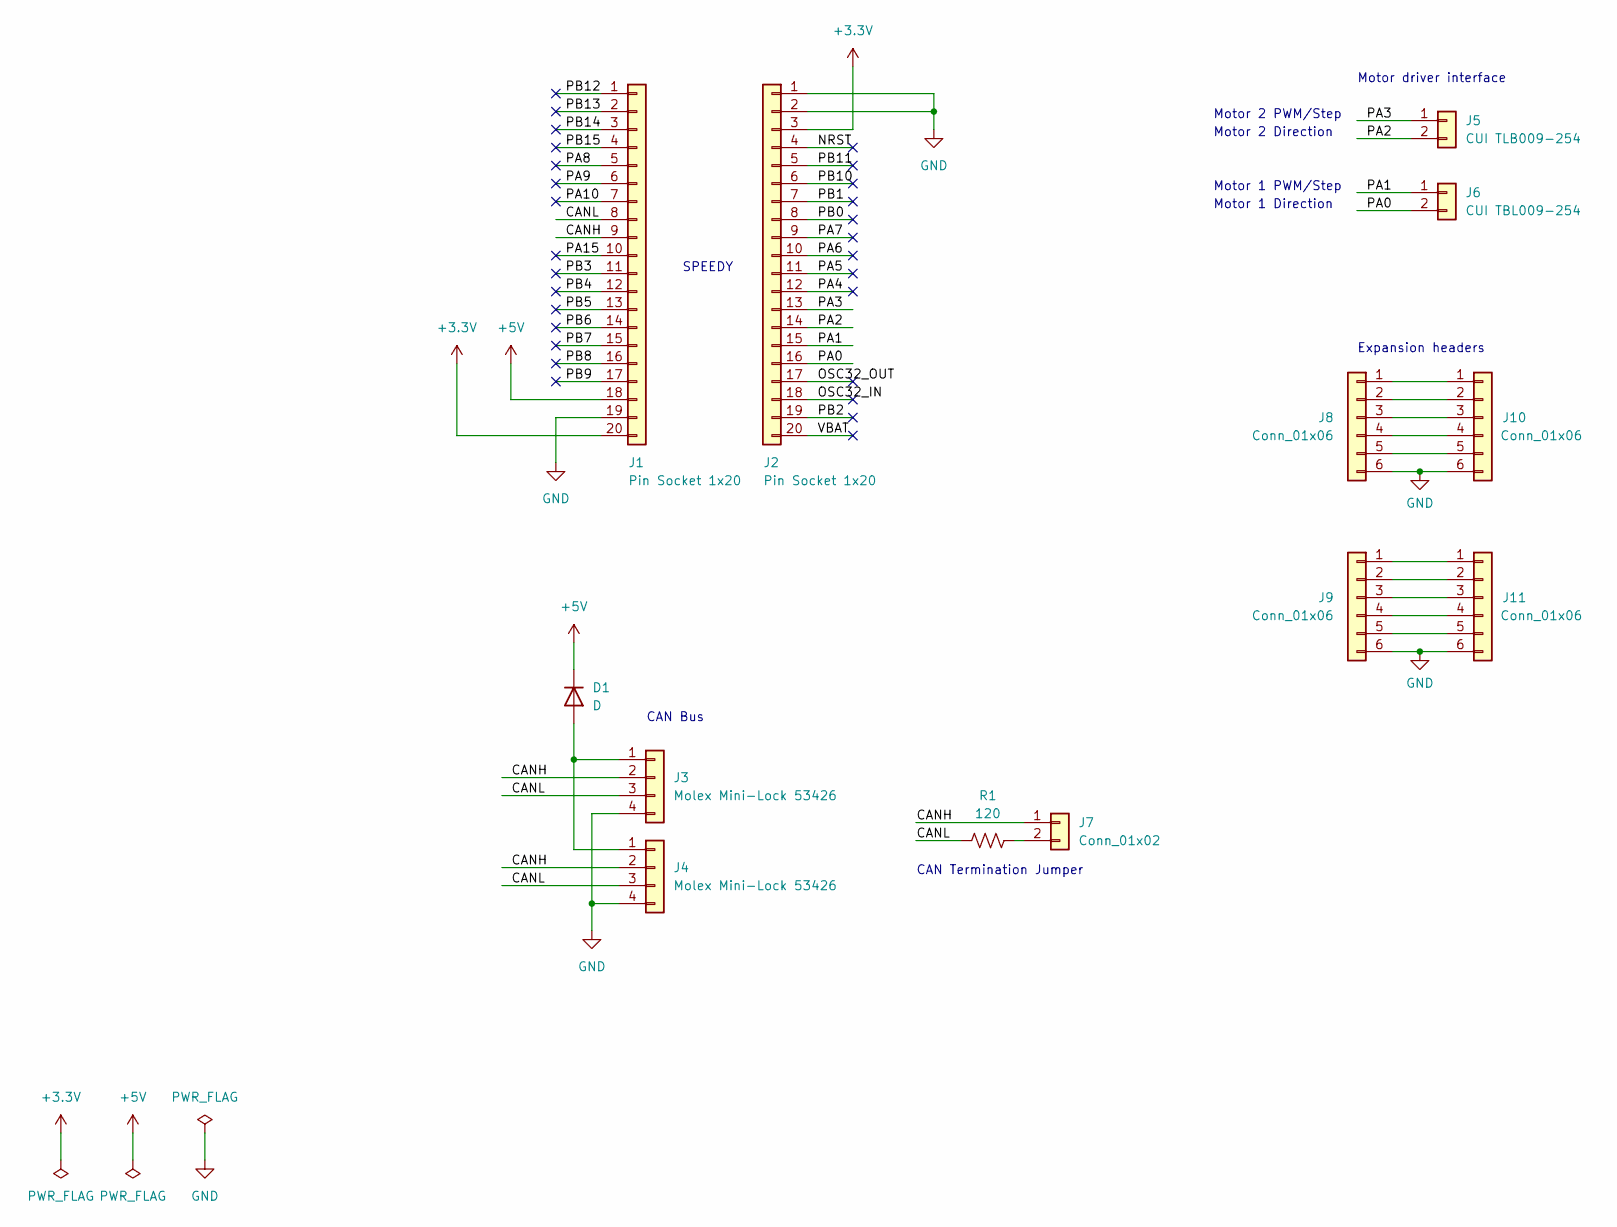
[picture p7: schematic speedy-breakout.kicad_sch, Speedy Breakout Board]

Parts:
D1: D; D_SMA
J1, J2: Pin Socket 1x20; PinSocket_1x20_P2.54mm_Vertical
J3, J4: Molex Mini-Lock 53426; Molex_Mini-Lock_53426-0410_1x04_P2.50mm_Horizontal
J5: CUI TLB009-254; TerminalBlock_CUI_TBL009-254-02_1x04_P2.54mm_Horizontal
J6: CUI TBL009-254; TerminalBlock_CUI_TBL009-254-02_1x04_P2.54mm_Horizontal
J7: Conn_01x02; PinHeader_1x02_P2.54mm_Vertical
J8, J9, J10, J11: Conn_01x06; PinHeader_1x06_P2.54mm_Vertical
R1: 120; R_0805_2012Metric_Pad1.20x1.40mm_HandSolder

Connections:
+3.3V: J1.20, J2.3
+5V: D1.1 (K), J1.18
/CANH: J1.9, J3.2, J4.2, J7.1
/CANL: J1.8, J3.3, J4.3, R1.1
/NRST: J2.4
/OSC32_IN: J2.18
/OSC32_OUT: J2.17
/PA0: J2.16, J6.2
/PA1: J2.15, J6.1
/PA2: J2.14, J5.2
/PA3: J2.13, J5.1
/PA4: J2.12
/PA5: J2.11
/PA6: J2.10
/PA7: J2.9
/PA8: J1.5
/PA9: J1.6
/PA10: J1.7
/PA15: J1.10
/PB0: J2.8
/PB1: J2.7
/PB2: J2.19
/PB3: J1.11
/PB4: J1.12
/PB5: J1.13
/PB6: J1.14
/PB7: J1.15
/PB8: J1.16
/PB9: J1.17
/PB10: J2.6
/PB11: J2.5
/PB12: J1.1
/PB13: J1.2
/PB14: J1.3
/PB15: J1.4
/VBAT: J2.20
GND: J1.19, J2.1, J2.2, J3.4, J4.4, J8.6, J9.6, J10.6, J11.6
unnamed: D1.2 (A), J3.1, J4.1
unnamed: J7.2, R1.2
unnamed: J8.1, J10.1
unnamed: J8.2, J10.2
unnamed: J8.3, J10.3
unnamed: J8.4, J10.4
unnamed: J8.5, J10.5
unnamed: J9.1, J11.1
unnamed: J9.2, J11.2
unnamed: J9.3, J11.3
unnamed: J9.4, J11.4
unnamed: J9.5, J11.5

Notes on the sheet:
Motor 2 Direction
Motor 2 PWM/Step
Motor 1 PWM/Step
SPEEDY
CAN Termination Jumper
CAN Bus
Expansion headers
Motor driver interface
Motor 1 Direction

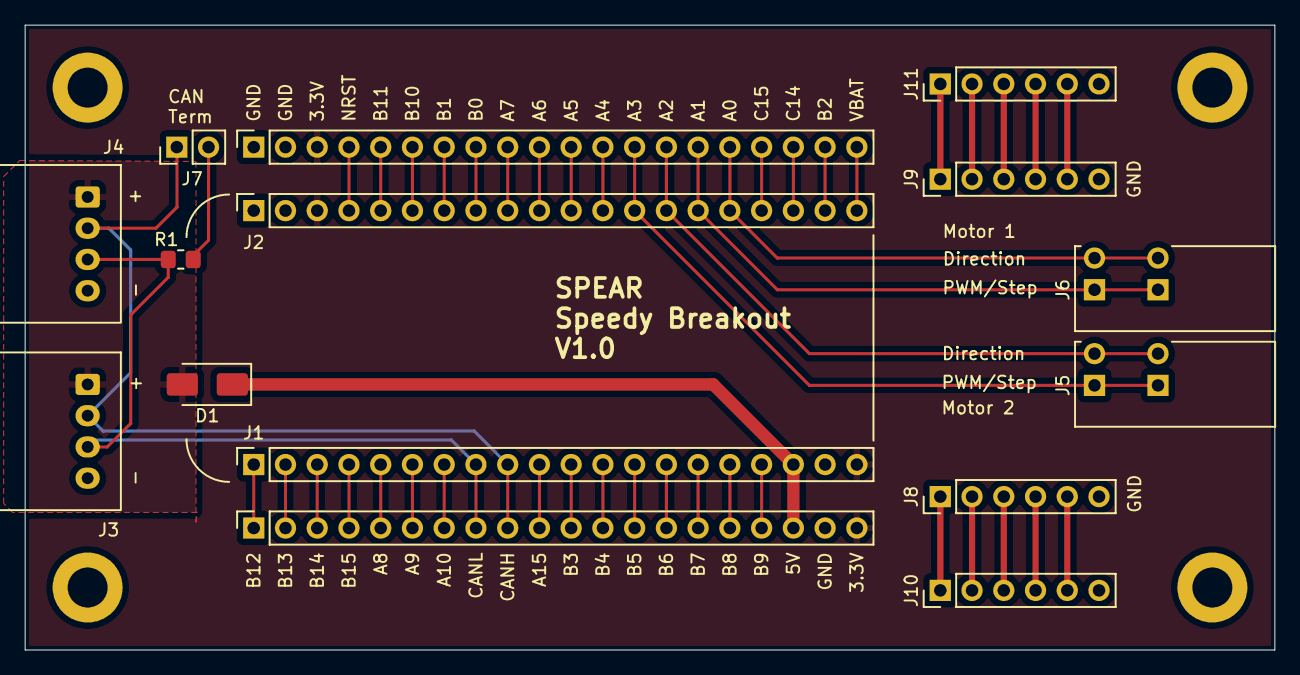
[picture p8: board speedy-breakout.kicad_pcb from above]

Board: 2 copper layers, 100.0 x 50.0 mm, 13 parts (0 on the bottom side), 21 nets.

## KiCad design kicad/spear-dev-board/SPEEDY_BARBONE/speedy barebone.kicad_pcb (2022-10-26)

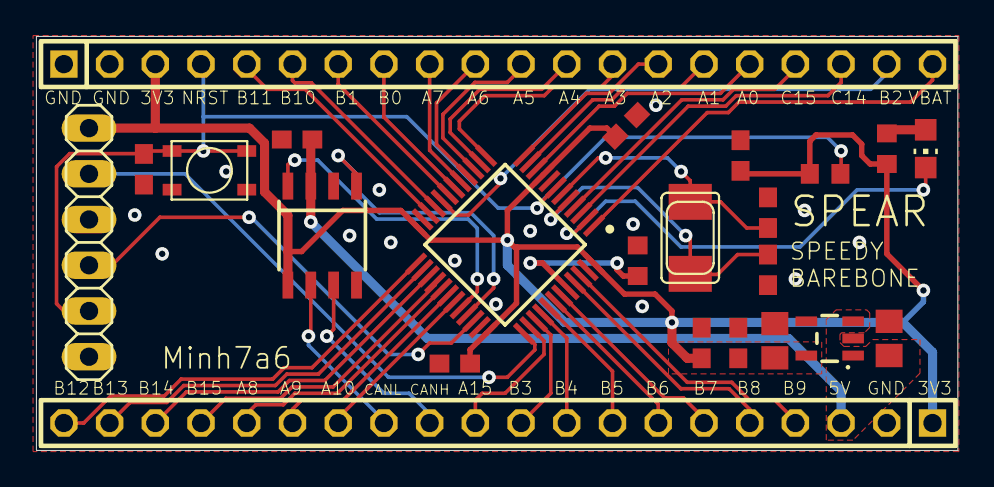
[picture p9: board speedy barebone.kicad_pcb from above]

Board: 2 copper layers, 51.2 x 23.0 mm, 23 parts (0 on the bottom side), 46 nets.

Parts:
C1, C2: 10uF; C0805
C3, C7, C10, C14, C15, C16, C17: 100nF; C0603
C4, C5: 22pF; C0603
IC2: STM32F103C8T6; QFP50P900X900X160-48N
JP1, JP2: 1X20
JP3: 1X06
LED2: CHIP-LED0805
R1: 100k; R0603
R8: 10k; R0603
R10: 1k; R0603
U1: 3.3V; SOT23-5
U$1: MCP2562-E/SN; SOIC8
U$2: 4.2X3.25-TACTILE-SWITCH; 4.2X3.25
X1: 8MHz; NX5032

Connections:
3.3V: C2.1, C3.1, C14.1, C15.1, C16.1, C17.1, IC2.9, IC2.24, IC2.36, IC2.48, JP1.1, JP2.3, JP3.6, R8.2, R10.1, U1.5, U$1.5
5V: C1.1, C7.1, JP1.3, U1.1, U1.3, U$1.3
BOOT0: IC2.44, R1.1
CANH: JP1.12, U$1.7
CANL: JP1.13, U$1.6
GND: C1.2, C2.2, C3.2, C4.2, C5.2, C7.2, C10.2, C14.2, C15.2, C16.2, C17.2, IC2.8, IC2.23, IC2.35, IC2.47, JP1.2, JP2.1, JP2.2, JP3.4, R1.2, U1.2, U$1.2, U$1.8, U$2.P$3, U$2.P$4
unnamed: LED2.A, R10.2
NRST: C10.1, IC2.7, JP2.4, JP3.2, R8.1, U$2.P$1, U$2.P$2
OSC32_IN: IC2.3, JP2.18
OSC32_OUT: IC2.4, JP2.17
OSC_IN: C4.1, IC2.5, X1.P$1
OSC_OUT: C5.1, IC2.6, X1.P$2
PA0-WKUP: IC2.10, JP2.16
PA1: IC2.11, JP2.15
PA2: IC2.12, JP2.14
PA3: IC2.13, JP2.13
PA4: IC2.14, JP2.12
PA5: IC2.15, JP2.11
PA6: IC2.16, JP2.10
PA7: IC2.17, JP2.9
PA8: IC2.29, JP1.16
PA9: IC2.30, JP1.15
PA10: IC2.31, JP1.14
PA11: IC2.32, U$1.4
PA12: IC2.33, U$1.1
PA15: IC2.38, JP1.11
PB0: IC2.18, JP2.8
PB1: IC2.19, JP2.7
PB2: IC2.20, JP2.19
PB3_SWO: IC2.39, JP1.10
PB4: IC2.40, JP1.9
PB5: IC2.41, JP1.8
PB6: IC2.42, JP1.7
PB7: IC2.43, JP1.6
PB8: IC2.45, JP1.5
PB9: IC2.46, JP1.4
PB10: IC2.21, JP2.6
PB11: IC2.22, JP2.5
PB12: IC2.25, JP1.20
PB13: IC2.26, JP1.19
PB14: IC2.27, JP1.18
PB15: IC2.28, JP1.17
PC13: IC2.2, LED2.C
SWCLK: IC2.37, JP3.5
SWDIO: IC2.34, JP3.3
VBAT: IC2.1, JP2.20

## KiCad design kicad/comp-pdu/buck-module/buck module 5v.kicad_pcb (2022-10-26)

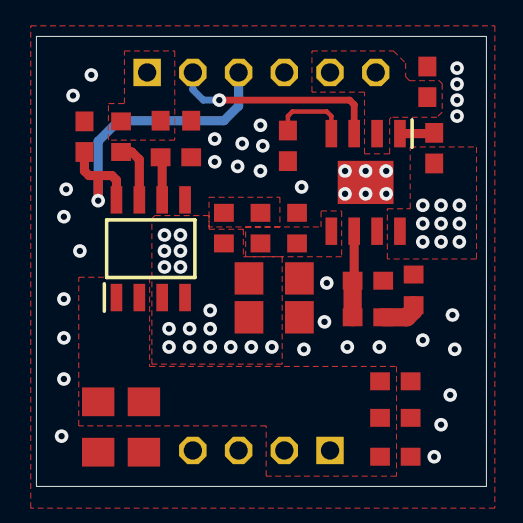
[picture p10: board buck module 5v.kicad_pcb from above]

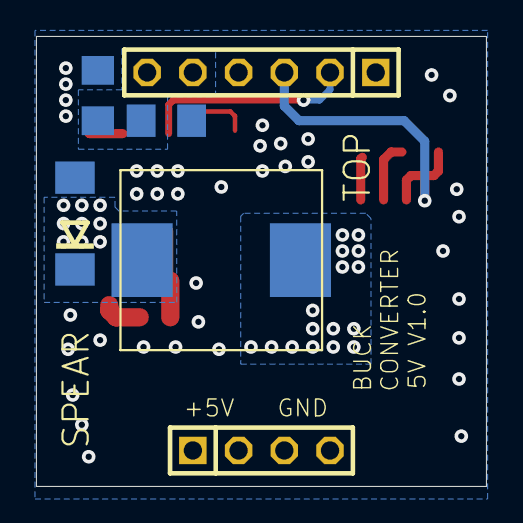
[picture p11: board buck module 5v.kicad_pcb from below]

Board: 2 copper layers, 25.0 x 25.0 mm, 28 parts (6 on the bottom side), 16 nets.

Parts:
C1, C2, C11, C12, C14: 100nF; C0603
C3, C4, C8, C9, C10, C15: 10uF; C1206
C5, C16: 10nF; C0603
C6: 22pF; C0603
C7: 2200pF; C0603
C13: 1nF; C0603
D1: DO214AA
IC1: TPS54531DDA; SOIC127P600X170-9N
IC2: ACS712ELCTR-20A-T; SOIC127P600X175-8N
JP1: 1X04
JP2: 1X06
R1: 37.4k; R0603
R2: 51.1; R0603
R3: 200k; R0603
R4: 39k; R0603
R5: 7.5k; R0603
R6: 10k; R0603
U$1: 10uH; 22UH-1040-5A

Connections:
+5V: C14.1, IC2.8, JP2.3
AIOUT: JP2.1, R5.1, R6.2
EN: IC1.3, JP2.2
GND: C2.2, C3.2, C4.2, C5.2, C6.2, C8.2, C9.2, C10.2, C11.2, C12.2, C13.2, C14.2, C15.2, C16.2, D1.A, IC1.7, IC1.9, IC2.5, JP1.3, JP1.4, JP2.4, R1.1, R4.1, R6.1
unnamed: C1.2, IC1.1
unnamed: C1.1, D1.C, IC1.8, U$1.P$1
unnamed: C7.2, R1.2
unnamed: C2.1, IC1.4
unnamed: C6.1, C7.1, IC1.6
unnamed: C13.1, IC2.6
unnamed: R2.1, R3.2
unnamed: IC1.5, R3.1, R4.2
SW: C8.1, C9.1, IC2.3, IC2.4, R2.2, U$1.P$2
VIN: C3.1, C4.1, C5.1, IC1.2, JP2.5, JP2.6
VIOUT: IC2.7, R5.2
VOUT: C10.1, C11.1, C12.1, C15.1, C16.1, IC2.1, IC2.2, JP1.1, JP1.2

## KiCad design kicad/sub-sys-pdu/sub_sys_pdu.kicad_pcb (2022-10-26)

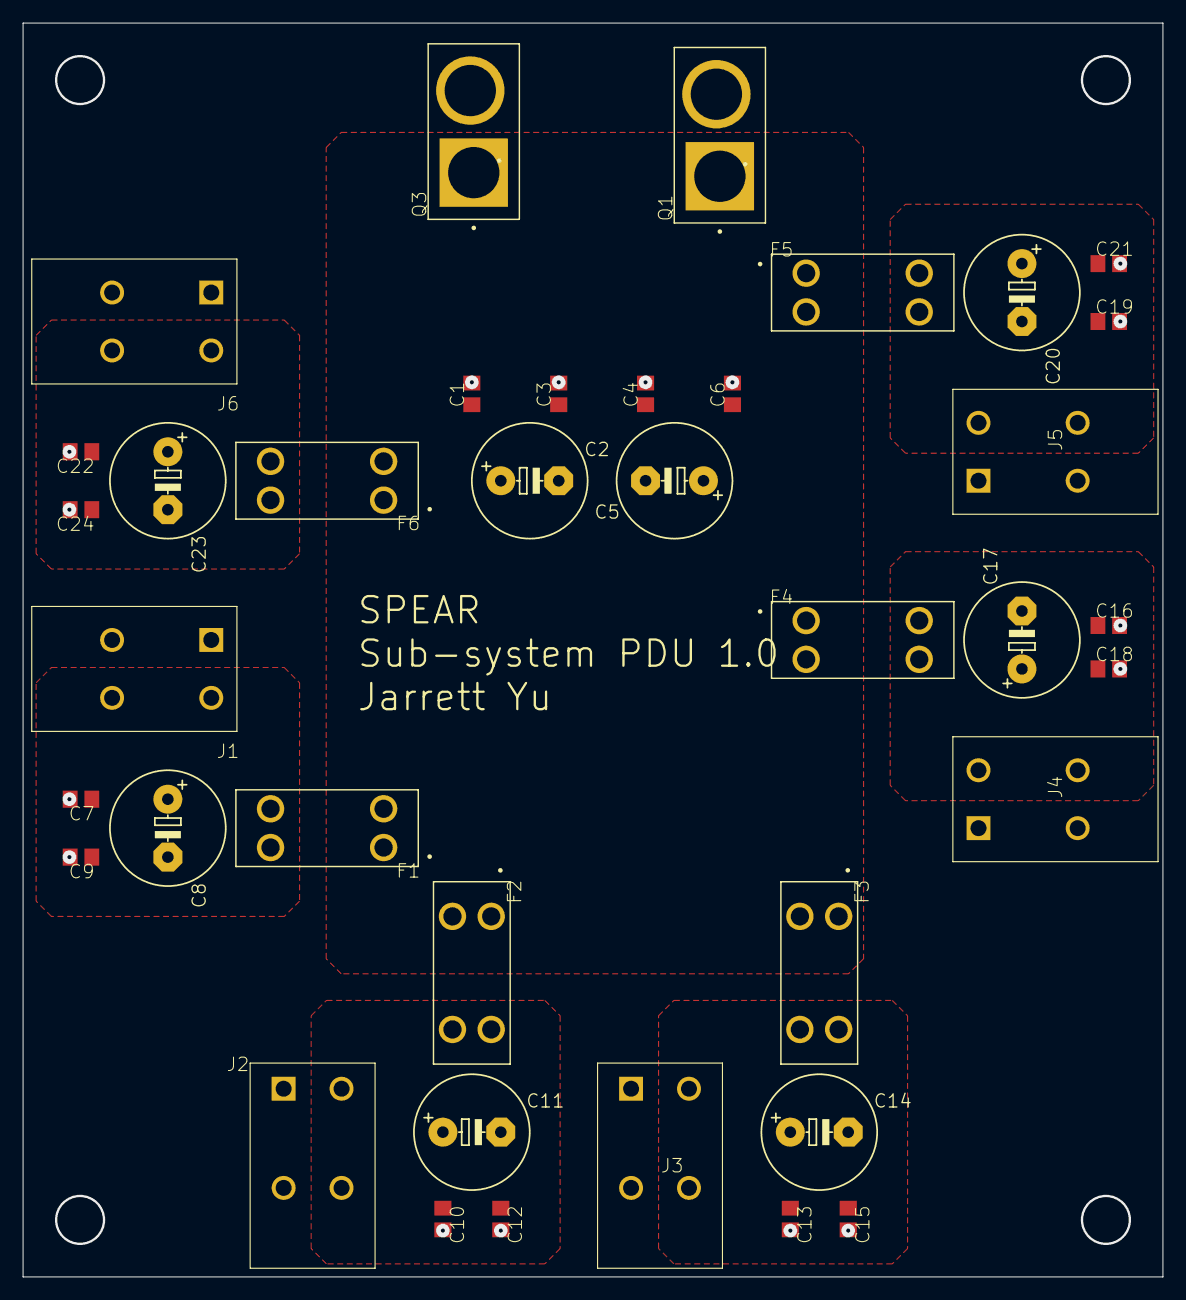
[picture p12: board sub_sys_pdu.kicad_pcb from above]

Board: 2 copper layers, 100.0 x 110.0 mm, 38 parts (0 on the bottom side), 8 nets, no tracks yet.

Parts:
C1, C3, C4, C6, C7, C9, C10, C12, C13, C15, C16, C18, C19, C21, C22, C24: 100nF; C0805
C2, C5, C8, C11, C14, C17, C20, C23: 100uf; E5-10,5
F1, F2, F3, F4, F5, F6: 3568; FUSE_3568
J1, J2, J3, J4, J5, J6: 1017503
Q1, Q3: XT60_YELLOW; AMASS_XT60PB-M

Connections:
GND: C1.2, C2.-, C3.2, C4.2, C5.-, C6.2, C7.2, C8.-, C9.2, C10.2, C11.-, C12.2, C13.2, C14.-, C15.2, C16.2, C17.-, C18.2, C19.2, C20.-, C21.2, C22.2, C23.-, C24.2, J1.1, J1.2, J2.1, J2.2, J3.1, J3.2, J4.1, J4.2, J5.1, J5.2, J6.1, J6.2, Q1.2, Q3.2
unnamed: C7.1, C8.+, C9.1, F1.2, F1.4, J1.3, J1.4
unnamed: C10.1, C11.+, C12.1, F2.2, F2.4, J2.3, J2.4
unnamed: C13.1, C14.+, C15.1, F3.2, F3.4, J3.3, J3.4
unnamed: C16.1, C17.+, C18.1, F4.2, F4.4, J4.3, J4.4
unnamed: C19.1, C20.+, C21.1, F5.2, F5.4, J5.3, J5.4
unnamed: C22.1, C23.+, C24.1, F6.2, F6.4, J6.3, J6.4
VCC: C1.1, C2.+, C3.1, C4.1, C5.+, C6.1, F1.1, F1.3, F2.1, F2.3, F3.1, F3.3, F4.1, F4.3, F5.1, F5.3, F6.1, F6.3, Q1.1, Q3.1

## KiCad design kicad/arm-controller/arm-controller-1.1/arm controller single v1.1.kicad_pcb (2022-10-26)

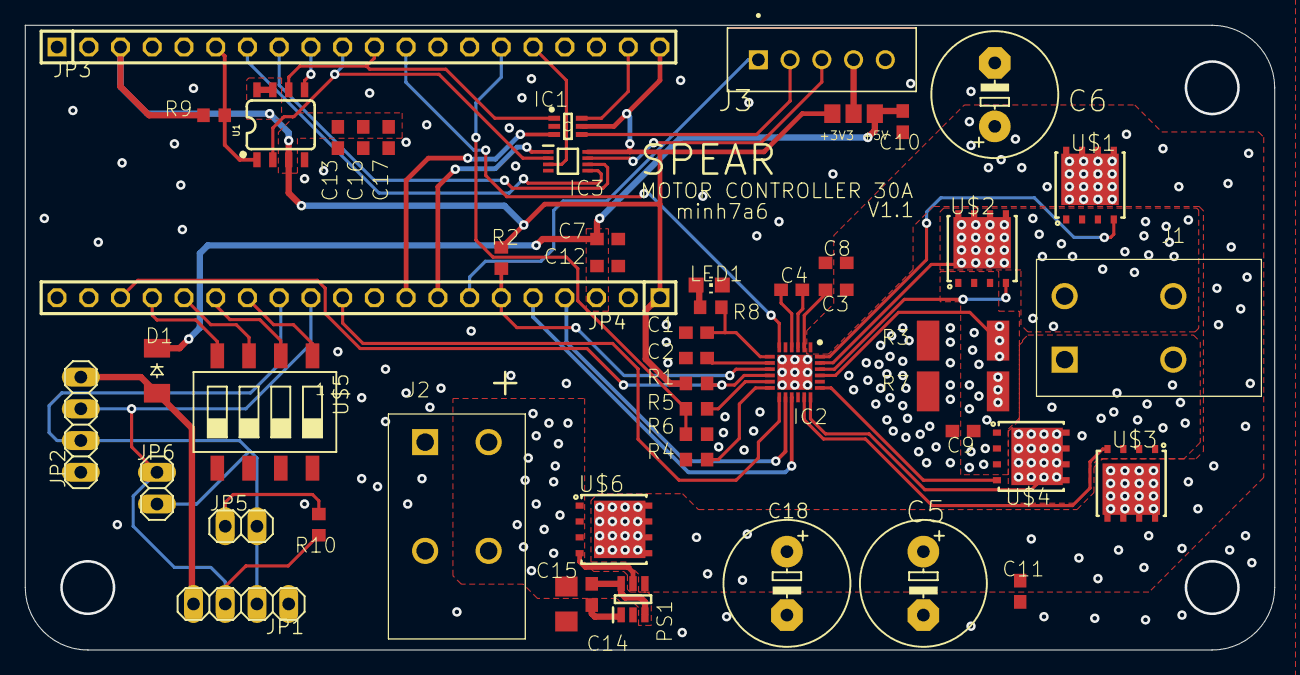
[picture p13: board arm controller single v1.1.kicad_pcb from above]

Board: 2 copper layers, 100.0 x 50.0 mm, 51 parts (0 on the bottom side), 51 nets.

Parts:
C1, C2, C3: 1uF; C0603
C4, C7, C8, C10, C11, C12, C13, C14, C16, C17: 100nF; C0603
C5, C6, C18: 680uF; E5-10,5
C9: 1000pF; C0603
C15: 10uF; C1206
D1: CGRM4001-G; SOD-123_MINI-SMA
IC1: NC7SZ157P6X; SOT65P210X110-6N
IC2: DRV8701PRGER; QFN50P400X400X100-25N
IC3: TS5A3357DCUT; SOP50P310X90-8N
J1, J2: 1017503
J3: 5-103669-4; TE_5-103669-4
JMP1: 0R-JUMPB; B0R-JMP
JP1, JP2: 1X04
JP3, JP4: 1X20
JP5, JP6: 1X02
LED1: CHIP-LED0805
PS1: PLM74700QDBVTQ1; SOT95P280X145-6N
R1, R2, R6, R9: 10k; R0603
R3, R7: 0.01; R2512
R4: 33k; R0603
R5: 7.5k; R0603
R8: 1k; R0603
R10: 120; R0603
U1: 4MB Flash; SO08
U$1, U$2, U$3, U$4, U$6: MOSFET-NCHDFN8-5X6; ALOM_DFN5X6_8L_EP1_P
U$5: SMS-004

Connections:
+3V3: C13.1, C16.1, C17.1, IC1.5, IC3.8, JMP1.3, JP3.3, JP3.20, JP4.1, R1.2, R2.2, R9.2, U1.3, U1.7, U1.8
+5V: C7.1, C10.1, C12.1, D1.C, JMP1.1, JP4.3
+5V/3V: J3.4, JMP1.2
CANH: JP1.3, JP2.3, JP4.12, JP6.1, R10.1
CANL: JP1.2, JP2.2, JP4.13, JP5.2, JP6.2
DAC: IC2.6, JP3.12
FAULT: IC2.9, JP4.6, R2.1
GH1: IC2.17, U$3.4
GH2: IC2.24, U$1.4
GL1: IC2.19, U$4.4
GL2: IC2.22, U$2.4
GND: C1.2, C2.2, C5.-, C6.-, C7.2, C8.2, C9.2, C10.2, C11.2, C12.2, C13.2, C15.2, C16.2, C17.2, C18.-, IC1.2, IC2.5, IC2.16, IC2.20, IC2.25, IC3.4, J2.1, J2.2, J3.5, JP1.1, JP2.1, JP3.1, JP3.2, JP4.2, LED1.C, PS1.2, R3.1, R4.1, R6.2, R7.1, U1.4, U$5.5, U$5.6, U$5.7, U$5.8
IDRIVE: IC2.12, R4.2
IN1: IC2.15, JP4.5
IN2: IC2.14, JP4.4
MISO: IC3.2, JP3.10, U1.2
MOSI: JP3.9, U1.5
MUX: IC3.7, J3.3
MUX2: IC1.4, J3.2
unnamed: D1.A, JP1.4, JP2.4
unnamed: LED1.A, R8.1
unnamed: PS1.5, U$6.4
unnamed: C1.1, IC2.7, R8.2
unnamed: C2.1, IC2.8
unnamed: C3.2, IC2.2
unnamed: C4.1, IC2.3
unnamed: C4.2, IC2.4
unnamed: JP5.1, R10.2
unnamed: IC2.11, R5.1
unnamed: C14.1, C15.1, J2.3, J2.4, PS1.3, PS1.6, U$6.1, U$6.2, U$6.3
unnamed: C14.2, PS1.1
NODE1: JP4.14, U$5.1
NODE2: JP4.15, U$5.2
NODE3: JP4.16, U$5.3
NODE4: JP4.17, U$5.4
PA0: IC3.3, JP3.16
PB0: IC3.6, JP3.8
PB1: IC3.5, JP3.7
PB2: IC1.6, JP3.19
PB4: IC1.3, JP4.9
PB5: IC3.1, JP4.8
PB6: J3.1, JP4.7
PB10: JP3.6, R9.1, U1.1
SCK: IC1.1, JP3.11, U1.6
SH1: IC2.18, J1.1, J1.2, U$3.1, U$3.2, U$3.3, U$4.5, U$4.6, U$4.7, U$4.8, U$4.9
SH2: IC2.23, J1.3, J1.4, U$1.1, U$1.2, U$1.3, U$2.5, U$2.6, U$2.7, U$2.8, U$2.9
SLEEP: IC2.13, JP4.11
SNSOUT: IC2.10, JP4.18, R1.1
SO: JP3.15, R5.2, R6.1
SP: C9.1, IC2.21, R3.2, R7.2, U$2.1, U$2.2, U$2.3, U$4.1, U$4.2, U$4.3
VIN: C3.1, C5.+, C6.+, C8.1, C11.1, C18.+, IC2.1, PS1.4, U$1.5, U$1.6, U$1.7, U$1.8, U$1.9, U$3.5, U$3.6, U$3.7, U$3.8, U$3.9, U$6.5, U$6.6, U$6.7, U$6.8, U$6.9

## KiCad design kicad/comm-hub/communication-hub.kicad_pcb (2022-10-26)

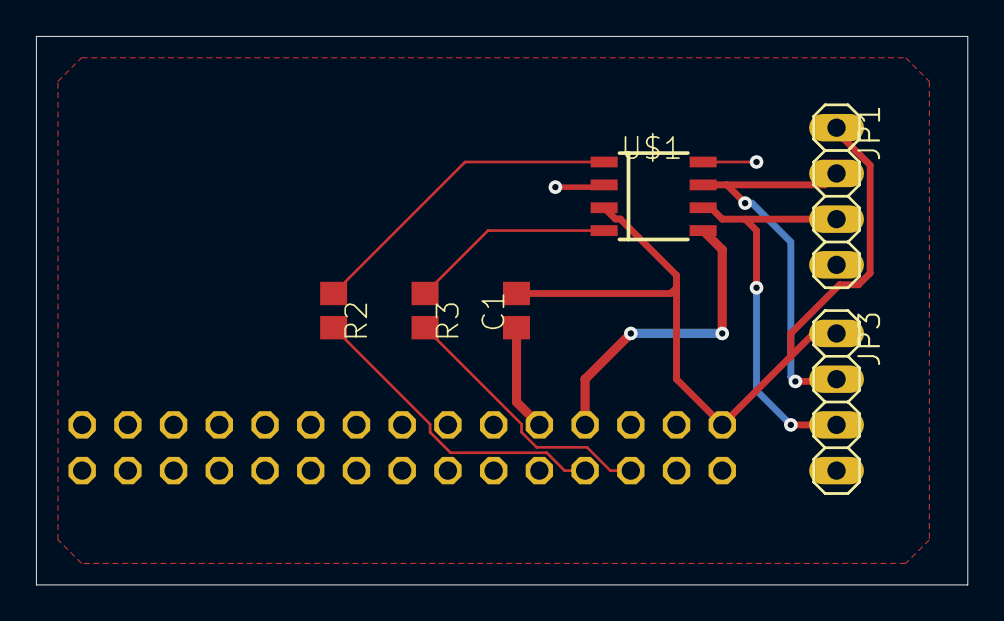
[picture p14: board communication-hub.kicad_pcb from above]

Board: 2 copper layers, 51.7 x 30.5 mm, 7 parts (1 on the bottom side), 9 nets.

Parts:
C1: 10uf; C0805
JP1, JP3: 1X04
JP2: 2X15
R2, R3: 220; R0805
U$1: MCP2562-E/SN; SOIC8

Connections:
+3V3: JP2.8, U$1.5
+5V: C1.2, JP1.1, JP2.2, JP3.1, U$1.3
CAN_H: JP1.2, JP3.2, U$1.7
CAN_L: JP1.3, JP3.3, U$1.6
CAN_RXD: JP2.5, R3.2
CAN_TXD: JP2.7, R2.2
GND: C1.1, JP1.4, JP2.10, JP2.11, JP2.21, JP3.4, U$1.2, U$1.8
unnamed: R3.1, U$1.4
unnamed: R2.1, U$1.1

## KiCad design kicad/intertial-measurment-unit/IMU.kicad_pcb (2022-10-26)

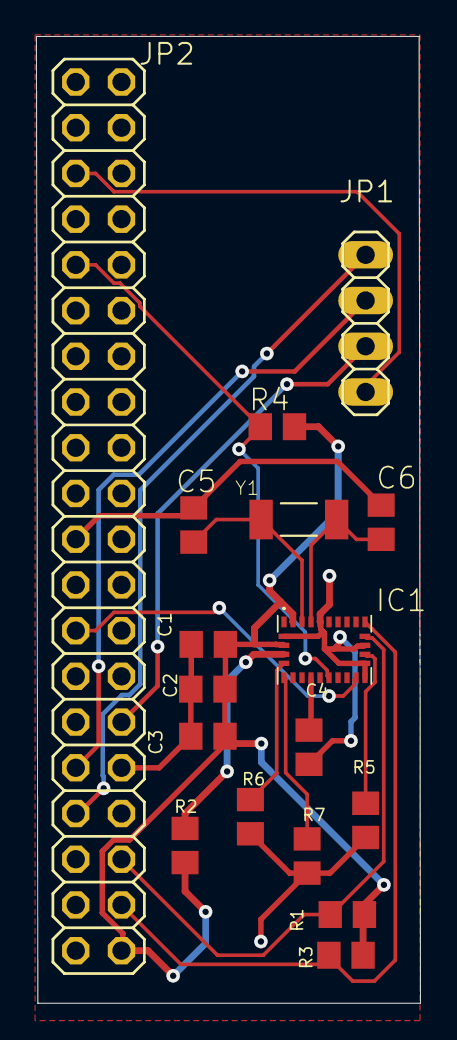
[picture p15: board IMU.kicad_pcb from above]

Board: 2 copper layers, 21.3 x 53.7 mm, 17 parts (0 on the bottom side), 17 nets.

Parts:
C1, C4: 100n; C0805
C2: 120n; C0805
C3: 6.8n; C0805
C5, C6: 22p; C0805
IC1: BNO055
JP1: 1X04
JP2: 2X20
R1, R2, R3, R4, R5, R6, R7: 10K; R0805
Y1: ECS-.327-12.5-39-TR

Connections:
+3V3: C1.1, C2.1, C3.1, IC1.3, IC1.28, JP2.1, R1.2, R2.2, R3.2, R4.2
ADD_SEL: IC1.17, R5.2
CAP: C4.1, IC1.9
GND: C1.2, C2.2, C3.2, C4.2, C5.1, C6.1, IC1.2, IC1.15, IC1.16, IC1.18, IC1.25, JP2.6, JP2.9, JP2.14, JP2.20, JP2.25, JP2.30, JP2.39, R5.1, R6.2, R7.2
INT: IC1.14, JP2.16
NBOOT: IC1.4, R2.1
NRESET: IC1.11, JP2.32, R4.1
PS0: IC1.6, R7.1
PS1: IC1.5, R6.1
SCL: IC1.19, JP2.5, R1.1
SDA: IC1.20, JP2.3, R3.1
UART_CTS: JP1.4, JP2.36
UART_RTS: JP1.3, JP2.11
UART_RX: JP1.2, JP2.10
UART_TX: JP1.1, JP2.8
XIN: C5.2, IC1.27, Y1.1
XOUT: C6.2, IC1.26, Y1.2

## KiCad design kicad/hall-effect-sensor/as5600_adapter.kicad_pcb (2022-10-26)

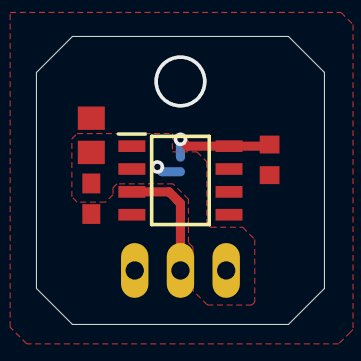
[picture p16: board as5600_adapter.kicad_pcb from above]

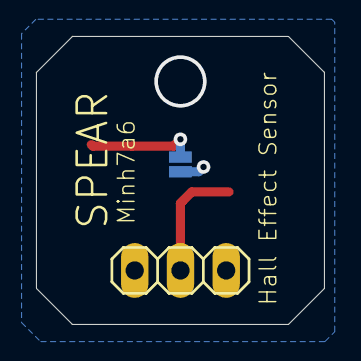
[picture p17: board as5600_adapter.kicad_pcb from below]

Board: 2 copper layers, 16.0 x 16.0 mm, 6 parts (2 on the bottom side), 4 nets.

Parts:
C1: 100nF; C0603
C2: 10uF; C0805
IC1: AS5600-ASOT; SOIC127P600X175-8N
JP1: 1X03
JP2: JUMPER-SMT_2_NC_PASTE_NO-SILK; SMT-JUMPER_2_NC_PASTE_NO-SILK
R1: 100K; R0603

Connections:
+3V3: C1.1, C2.1, IC1.1, IC1.2, JP1.3, JP2.2
GND: C1.2, C2.2, IC1.4, IC1.5, JP1.1, R1.1
unnamed: IC1.8, JP2.1, R1.2
OUT: IC1.3, JP1.2

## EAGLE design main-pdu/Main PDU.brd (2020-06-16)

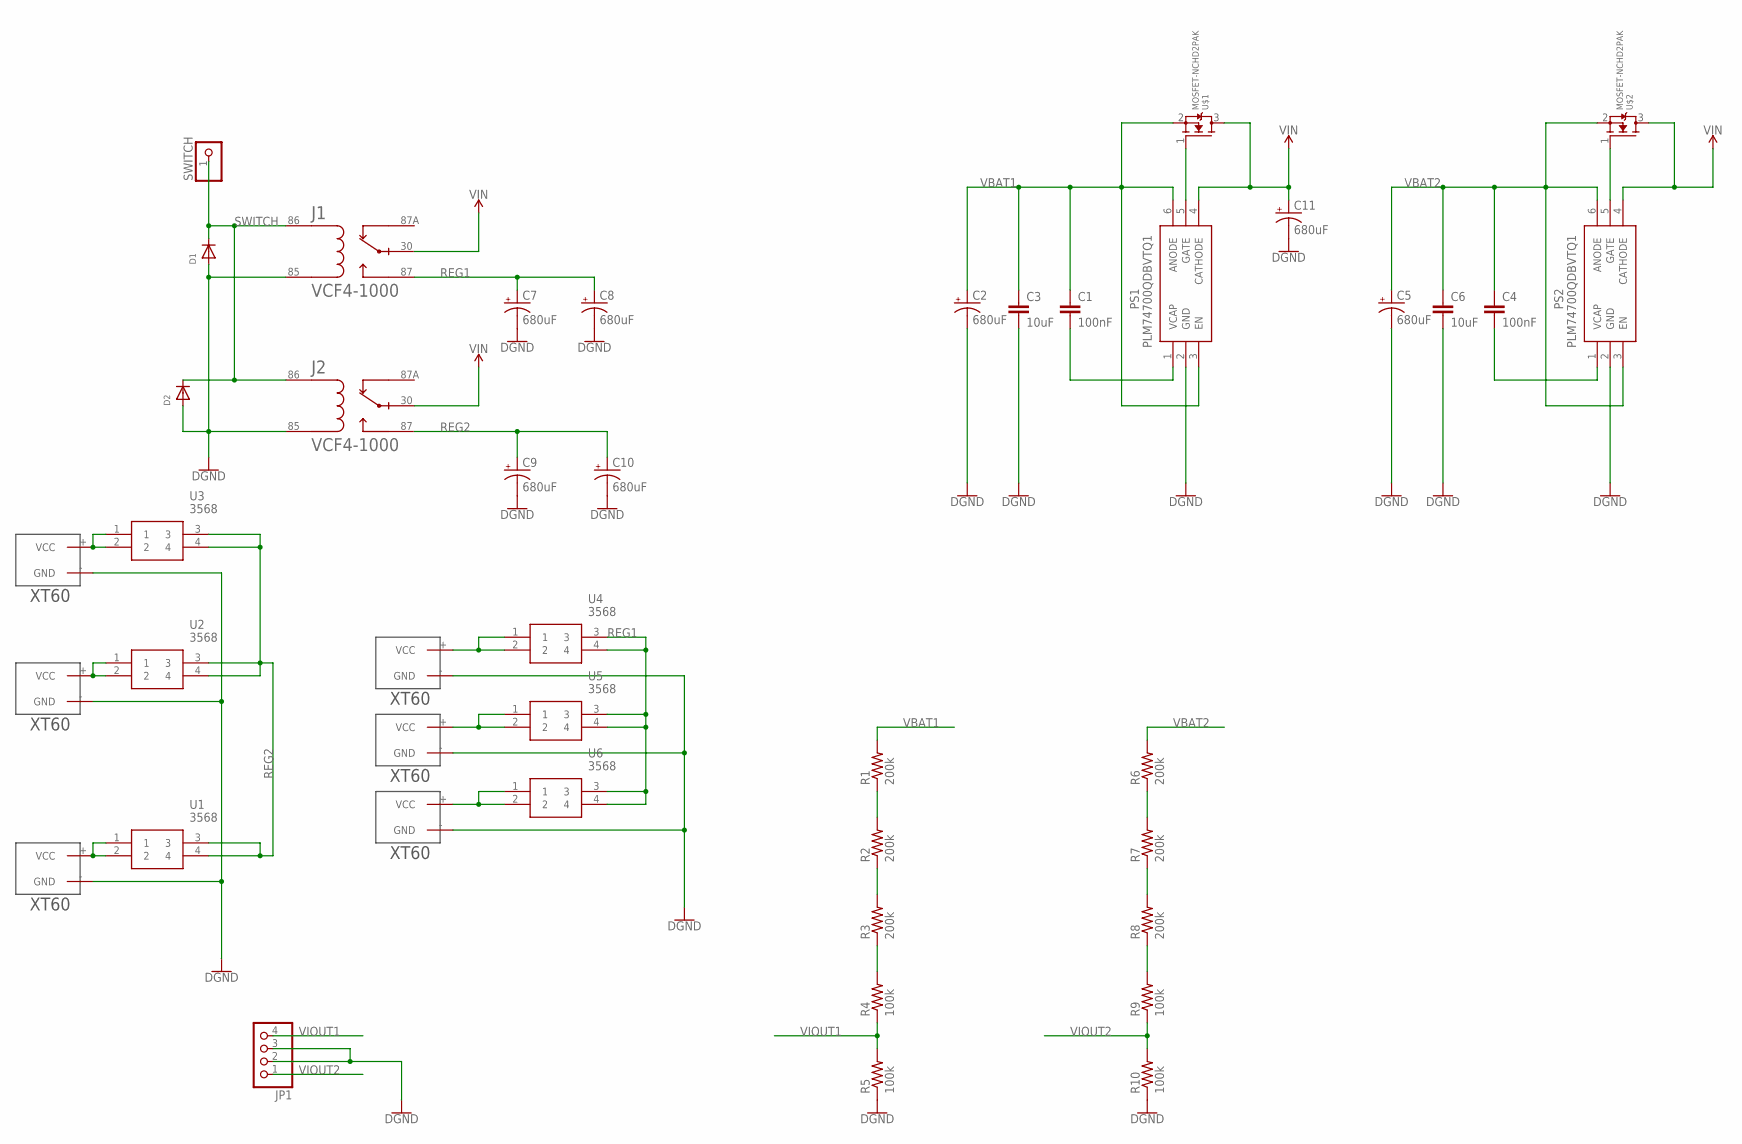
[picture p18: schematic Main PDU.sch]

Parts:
C1, C4: 100nF; C0805
C2, C5, C7, C8, C9, C10, C11: 680uF; E5-10,5
C3, C6: 10uF; C1206
D1, D2: DIODESOD-123; SOD-123
J1, J2: VCF4-1000; TE_VCF4-1000
JP1: PINHD-1X4; 1X04
PS1, PS2: PLM74700QDBVTQ1; SOT95P280X145-6N
R1, R2, R3, R6, R7, R8: 200k; R0805
R4, R5, R9, R10: 100k; R0805
SWITCH: PINHD-1X1; 1X01
U1, U2, U3, U4, U5, U6: 3568
U$1, U$2: MOSFET-NCHD2PAK; MBRB41H100CTT4G
U$3, U$4, U$6, U$7, U$8, U$10: XT60

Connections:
GND: C2.-, C3.2, C5.-, C6.2, C7.-, C8.-, C9.-, C10.-, C11.-, D1.A, D2.A, J1.85, J2.85, JP1.2, JP1.3, PS1.2 (GND), PS2.2 (GND), R5.1, R10.1, U$3.- (GND), U$4.- (GND), U$6.- (GND), U$7.- (GND), U$8.- (GND), U$10.- (GND)
unnamed: PS1.5 (GATE), U$1.1 (G)
unnamed: C1.2, PS1.1 (VCAP)
unnamed: R1.1, R2.2
unnamed: R2.1, R3.2
unnamed: C4.2, PS2.1 (VCAP)
unnamed: PS2.5 (GATE), U$2.1 (G)
unnamed: R3.1, R4.2
unnamed: R6.1, R7.2
unnamed: R7.1, R8.2
unnamed: R8.1, R9.2
unnamed: U1.1, U1.2, U$8.+ (VCC)
unnamed: U6.1, U6.2, U$4.+ (VCC)
unnamed: U3.1, U3.2, U$10.+ (VCC)
unnamed: U2.1, U2.2, U$7.+ (VCC)
unnamed: U5.1, U5.2, U$3.+ (VCC)
unnamed: U4.1, U4.2, U$6.+ (VCC)
REG1: C7.+, C8.+, J1.87, U4.3, U4.4, U5.3, U5.4, U6.3, U6.4
REG2: C9.+, C10.+, J2.87, U1.3, U1.4, U2.3, U2.4, U3.3, U3.4
SWITCH: D1.C, D2.C, J1.86, J2.86, SWITCH.1
VBAT1: C1.1, C2.+, C3.1, PS1.3 (EN), PS1.6 (ANODE), R1.2, U$1.2 (S)
VBAT2: C4.1, C5.+, C6.1, PS2.3 (EN), PS2.6 (ANODE), R6.2, U$2.2 (S)
VIN: C11.+, J1.30, J2.30, PS1.4 (CATHODE), PS2.4 (CATHODE), U$1.3 (D), U$2.3 (D)
VIOUT1: JP1.4, R4.1, R5.2
VIOUT2: JP1.1, R9.1, R10.2


Board: 2 copper layers, 100.0 x 96.0 mm, 43 parts (0 on the bottom side), 25 nets.

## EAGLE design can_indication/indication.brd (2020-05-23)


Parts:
C1, C2, C3, C4, C5, C9, C10, C11, C12, C13, C14: 100n; C0805
C6: 4u7; C0805
C7: 10n; C0805
C8: 1u; C0805
IC1, IC2: TPS92630QPWPRQ1; SOP65P640X120-17N
JP1: PINHD-1X2; 1X02
R1, R3: 10K; R0805
R2, R10: 815; R0805
R26, R27, R28: 10k; R0805
SV1, SV2: MA04-1
U$1: MCP2562-E/SN; SOIC8
U$2: STM-DEV-BOARD
U$3, U$5: R50RGB-4-0045
U$4: TE-CONN_5-103669-1

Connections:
+3V3: C1.1, C2.1, C3.1, C4.1, C5.1, C6.1, C7.1, C8.1, R26.2, R27.2, R28.2, U$1.5 (VIO), U$4.P$1 (1)
+5V: IC1.1 (VIN), IC2.1 (VIN), JP1.1, SV1.4, SV2.4, U$1.3 (VDD)
CANH: SV1.3, SV2.3, U$1.7 (CANH), U$2.CANH
CANL: SV1.2, SV2.2, U$1.6 (CANL), U$2.CANL
CAN_STBY: U$1.8 (STBY)
GND: C1.2, C2.2, C3.2, C4.2, C5.2, C6.2, C7.2, C8.2, C9.2, C10.2, C11.2, C12.2, C13.2, C14.2, IC1.9 (GND), IC2.9 (GND), JP1.2, R1.1, R2.1, R3.1, R10.1, SV1.1, SV2.1, U$1.2 (VSS), U$2.GND@2 (GND), U$2.GND@3 (GND), U$3.P$2 (C), U$4.P$2 (2), U$5.P$2 (C)
I2C_SCL: R27.1, U$2.PB14
I2C_SDA: R28.1, U$2.PB15
L1OUT1: C9.1, IC1.11 (VSNS1), IC1.16 (IOUT1), U$3.P$3 (BLU)
L1OUT2: C10.1, IC1.12 (VSNS2), IC1.15 (IOUT2), U$3.P$4 (RED)
L1OUT3: C11.1, IC1.13 (VSNS3), IC1.14 (IOUT3), U$3.P$1 (GRN)
L2OUT1: C12.1, IC2.11 (VSNS1), IC2.16 (IOUT1), U$5.P$3 (BLU)
L2OUT2: C13.1, IC2.12 (VSNS2), IC2.15 (IOUT2), U$5.P$4 (RED)
L2OUT3: C14.1, IC2.13 (VSNS3), IC2.14 (IOUT3), U$5.P$1 (GRN)
LED_!OE: R26.1, U$2.PB10
unnamed: IC1.10 (REF), R10.2
unnamed: IC2.8 (TEMP), R3.2
unnamed: IC2.10 (REF), R2.2
unnamed: IC1.8 (TEMP), R1.2
PA1: IC2.2 (EN), U$2.PA1
PA2: IC2.3 (PWM1), U$2.PA2
PA3: IC2.4 (PWM2), U$2.PA3
PA4: IC2.5 (PWM3), U$2.PA4
PA5: IC2.6 (FAULT), U$2.PA5
PA6: IC2.7 (FAULT_S), U$2.PA6
PB4: IC1.7 (FAULT_S), U$2.PB4
PB5: IC1.6 (FAULT), U$2.PB5
PB6: IC1.5 (PWM3), U$2.PB6
PB7: IC1.4 (PWM2), U$2.PB7
PB8: IC1.3 (PWM1), U$2.PB8
PB9: IC1.2 (EN), U$2.PB9
STM_CANRX: U$1.4 (RXD), U$2.PB13
STM_CANTX: U$1.1 (TXD), U$2.PB12

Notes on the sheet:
Pullup Resistors
Digital Supply Decoupling
4.7uF Capacitor must be connected to VDD_3
Analog Supply Decoupling
Pin 26
PIN 1


Board: 2 copper layers, 69.9 x 63.5 mm, 31 parts (1 on the bottom side), 32 nets.

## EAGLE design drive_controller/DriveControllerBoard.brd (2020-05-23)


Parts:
C2: 100nf; C0805
D1: CGRM4001-G; SOD-123_MINI-SMA
R3, R4, R5, R6: 10K; R0805
U$1, U$2, U$5, U$6: AMP-MTE-4MALE
U$3: STM-DEV-BOARD
U$4: AMP-MTE-2MALE

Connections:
1A: R3.1, U$2.1, U$3.PA5
1B: R4.1, U$2.2, U$3.PA6
2A: R5.1, U$1.1, U$3.PA2
2B: R6.1, U$1.2, U$3.PA3
+3V3: R3.2, R4.2, R5.2, R6.2, U$1.3, U$2.3, U$3.3.3V
+5V: C2.1, D1.A, D1.C, U$3.5V, U$5.1, U$6.1
CANH: U$3.CANH, U$5.2, U$6.2
CANL: U$3.CANL, U$5.3, U$6.3
GND: C2.2, U$1.4, U$2.4, U$3.GND, U$3.GND@2 (GND), U$3.GND@3 (GND), U$4.P$2, U$5.4, U$6.4
USART_3: U$3.PA4, U$4.P$1


Board: 2 copper layers, 47.7 x 91.0 mm, 12 parts (0 on the bottom side), 10 nets.

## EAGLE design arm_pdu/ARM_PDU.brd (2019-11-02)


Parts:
U$1, U$2, U$3, U$14, U$15, U$16: 20A_FUSE_HOLDER
U$4, U$5, U$6, U$7: PP45_HOR_2BOT
U$8: AMP-MTE-2MALE
U$9: R-78E3.3-0.5
U$10, U$11, U$12, U$13, U$17, U$18: 2PIN_5MM

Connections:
+VBAT: U$1.P$1 (1), U$2.P$1 (1), U$3.P$1 (1), U$4.+, U$5.+, U$6.+, U$7.+, U$9.+VIN (VIN), U$14.P$1 (1), U$15.P$1 (1), U$16.P$1 (1)
GND: U$4.-, U$5.-, U$6.-, U$7.-, U$8.P$2, U$9.GND, U$10.P$1 (1), U$11.P$1 (1), U$12.P$1 (1), U$13.P$2 (2), U$17.P$2 (2), U$18.P$2 (2)
unnamed: U$8.P$1, U$9.VOUT
OUT1: U$1.P$3 (2), U$13.P$1 (1)
OUT2: U$2.P$3 (2), U$17.P$1 (1)
OUT3: U$3.P$3 (2), U$18.P$1 (1)
OUT4: U$10.P$2 (2), U$16.P$3 (2)
OUT5: U$11.P$2 (2), U$15.P$3 (2)
OUT6: U$12.P$2 (2), U$14.P$3 (2)


Board: 2 copper layers, 100.0 x 100.0 mm, 18 parts (0 on the bottom side), 9 nets.

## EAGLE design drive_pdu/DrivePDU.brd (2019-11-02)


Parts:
U$1, U$2, U$3: PP45_HOR_4GRD
U$4, U$5, U$6, U$7: PP45_HOR_2BOT
U$8: AMP-MTE-2MALE
U$9: R-78E3.3-0.5
U$10, U$11, U$12, U$13, U$14, U$15, U$16, U$17: 30A_FUSE; 01220090Z

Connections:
+VFUSED: U$1.+_1 (+), U$1.+_2 (+), U$2.+_1 (+), U$2.+_2 (+), U$3.+_1 (+), U$3.+_2 (+), U$9.+VIN (VIN), U$10.P$1 (1), U$10.P$2 (1), U$11.P$1 (1), U$11.P$2 (1), U$12.P$1 (1), U$12.P$2 (1), U$13.P$1 (1), U$13.P$2 (1), U$14.P$1 (1), U$14.P$2 (1), U$15.P$1 (1), U$15.P$2 (1), U$16.P$1 (1), U$16.P$2 (1), U$17.P$1 (1), U$17.P$2 (1)
GND: U$1.-_1 (-), U$1.-_2 (-), U$2.-_1 (-), U$2.-_2 (-), U$3.-_1 (-), U$3.-_2 (-), U$4.-, U$5.-, U$6.-, U$7.-, U$8.P$2, U$9.GND
unnamed: U$8.P$1, U$9.VOUT
unnamed: U$4.+, U$10.P$3 (2), U$10.P$4 (2), U$11.P$3 (2), U$11.P$4 (2)
unnamed: U$7.+, U$16.P$3 (2), U$16.P$4 (2), U$17.P$3 (2), U$17.P$4 (2)
unnamed: U$5.+, U$14.P$3 (2), U$14.P$4 (2), U$15.P$3 (2), U$15.P$4 (2)
unnamed: U$6.+, U$12.P$3 (2), U$12.P$4 (2), U$13.P$3 (2), U$13.P$4 (2)


Board: 2 copper layers, 100.1 x 100.3 mm, 17 parts (0 on the bottom side), 7 nets.

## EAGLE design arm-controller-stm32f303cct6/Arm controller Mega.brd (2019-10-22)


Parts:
C1, C6, C7, C8, C9, C15: 100nF; C0805
C2, C3: 22pF; C0805
C4, C5: 10uF; C0805
C10, C14: 33nF; C0805
C11, C12, C13: 100uF; 153CLV-0810
C16, C17: 0u1; C0805
CON1, CON2: SM04B-GHS-TB
FB1: 30O/1.8A; 0603
J1, J2, J3, J6: CONN_025MM; SCREWTERMINAL-5MM-2
J4, J5: 5-103669-4; TE_5-103669-4
JP1: CORTEX-M-DBG; FTSH-105-01-F-DV-007
JP2, JP3, JP4, JP5, JP6, JP7, JP8, JP9, JP10, JP11, JP12, JP13, JP14, JP15: JUMPER-SMT_2_NO_NO-SILK; SMT-JUMPER_2_NO_NO-SILK
LED1: LEDCHIPLED_0805; CHIPLED_0805
R1, R3, R5, R6, R8, R9, R10, R15: 10k; R0805
R2, R4, R7, R11, R12, R13, R14, R16, R17: 1k; R0805
S1: MOMENTARY-SWITCH-SPST-2-SMD-5.2MM; TACTILE_SWITCH_SMD_5.2MM
U1: STM32F303RET6; LQFP64-10X10MM
U2: 3.3V; SOT23-5
U$1, U$2: VNH5019; MULTIPOWERSO-30
U$3, U$4: MOSFET-NCH; TO252-3
U$5: MCP2562-E/SN; SOIC8
U$6: SMS-004
X1: 8MHz; NX5032

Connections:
+3V3: C5.1, C6.1, C7.1, C8.1, C9.1, C17.1, FB1.1, JP1.1 (VCC), JP2.2, JP4.2, LED1.A, R3.1, R5.2, R6.2, R8.2, R9.2, U1.1 (VBAT), U1.19 (VDD), U1.32 (VDD), U1.48 (VDD), U1.64 (VDD), U2.5 (OUT), U$5.5 (VIO), U$6.5, U$6.6, U$6.7, U$6.8
+5V: C4.1, C16.1, CON1.P$1, CON2.P$1, JP3.2, JP6.2, U2.1 (IN), U2.3 (EN), U$5.3 (VDD)
CANH: CON1.P$2, CON2.P$2, U$5.7 (CANH)
CANL: CON1.P$3, CON2.P$3, U$5.6 (CANL)
CAN_RX: U1.44 (PA11), U$5.4 (RXD)
CAN_TX: U1.45 (PA12), U$5.1 (TXD)
CS1: C10.1, R10.2, U1.10 (PC2)
CS2: C14.1, R15.2, U1.11 (PC3)
ENA1: R12.1, U1.38 (PC7)
ENA2: R16.2, U1.35 (PB14)
ENB1: R13.1, U1.37 (PC6)
ENB2: R17.2, U1.34 (PB13)
GND: C1.2, C2.2, C3.2, C4.2, C5.2, C6.2, C7.2, C8.2, C9.2, C10.2, C11.-, C12.-, C13.-, C14.2, C15.2, C16.2, C17.2, CON1.P$4, CON1.P$5, CON1.P$6, CON2.P$4, CON2.P$5, CON2.P$6, J1.1, J4.5, J5.5, J6.1, JP1.3 (GND_1), JP1.5 (GND_2), JP1.9 (GND_DETECT), R1.2, R2.1, R11.2, R14.2, S1.3, S1.4, U1.12 (VSSA), U1.18 (VSS), U1.31 (VSS), U1.47 (VSS), U1.63 (VSS), U2.2 (GND), U$1.2 (GNDA), U$1.14 (GNDB), U$1.17 (GNDB), U$1.18 (GNDB), U$1.19 (GNDB), U$1.20 (GNDB), U$1.22 (GNDA), U$1.24 (GNDB), U$1.26 (GNDA), U$1.27 (GNDA), U$1.28 (GNDA), U$1.29 (GNDA), U$2.2 (GNDA), U$2.14 (GNDB), U$2.17 (GNDB), U$2.18 (GNDB), U$2.19 (GNDB), U$2.20 (GNDB), U$2.22 (GNDA), U$2.24 (GNDB), U$2.26 (GNDA), U$2.27 (GNDA), U$2.28 (GNDA), U$2.29 (GNDA), U$5.2 (VSS), U$5.8 (STBY)
INA1: U1.43 (PA10), U$1.4 (INA)
INA2: U1.41 (PA8), U$2.4 (INA)
INB1: U1.42 (PA9), U$1.10 (INB)
INB2: U1.40 (PC9), U$2.10 (INB)
MISO: JP5.2, JP12.2, U1.56 (PB4)
unnamed: C1.1, FB1.2, U1.13 (VDDA)
unnamed: C2.1, U1.5 (PF0-OSC_IN), X1.P$1
unnamed: R1.1, U1.60 (BOOT0)
unnamed: J5.4, JP2.1, JP3.1
unnamed: LED1.C, R2.2
unnamed: R7.1, U$2.7 (PWM)
unnamed: R10.1, R11.1, U$1.8 (CS)
unnamed: R4.1, U$1.7 (PWM)
unnamed: R6.1, R12.2, U$1.5 (ENA/DIAGA)
unnamed: R5.1, R13.2, U$1.9 (ENB/DIAGB)
unnamed: R8.1, R16.1, U$2.5 (ENA/DIAGA)
unnamed: R9.1, R17.1, U$2.9 (ENB/DIAGB)
unnamed: R14.1, R15.1, U$2.8 (CS)
unnamed: U$1.11 (CP), U$4.1 (G)
unnamed: C3.1, U1.6 (PF1-OSC_OUT), X1.P$2
unnamed: U$2.11 (CP), U$3.1 (G)
unnamed: J4.4, JP4.1, JP6.1
unnamed: J4.2, JP9.1, JP10.1
unnamed: J4.3, JP5.1, JP7.1, JP8.1
unnamed: J5.3, JP11.1, JP12.1, JP13.1
unnamed: J5.2, JP14.1, JP15.1
NODE1: U1.27 (PB1), U$6.1
NODE2: U1.28 (PB2), U$6.2
NODE3: U1.29 (PB10), U$6.3
NODE4: U1.30 (PB11), U$6.4
OUTA1: J3.2, U$1.1 (OUTA), U$1.25 (OUTA), U$1.30 (OUTA), U$1.OUTA, U$1.OUTA@1 (OUTA)
OUTA2: J2.2, U$2.1 (OUTA), U$2.25 (OUTA), U$2.30 (OUTA), U$2.OUTA, U$2.OUTA@1 (OUTA)
OUTB1: J3.1, U$1.15 (OUTB), U$1.16 (OUTB), U$1.21 (OUTB), U$1.OUTB, U$1.OUTB@1 (OUTB)
OUTB2: J2.1, U$2.15 (OUTB), U$2.16 (OUTB), U$2.21 (OUTB), U$2.OUTB, U$2.OUTB@1 (OUTB)
PA6: JP7.2, U1.22 (PA6)
PA7: JP13.2, U1.23 (PA7)
PB5: JP9.2, U1.57 (PB5)
PB6: JP14.2, U1.58 (PB6)
PB8: JP11.2, U1.61 (PB8)
PB9: JP8.2, U1.62 (PB9)
PC11: J5.1, U1.52 (PC11)
PC12: J4.1, U1.53 (PC12)
PD2: U1.54 (PD2)
PWM1: R4.2, U1.39 (PC8)
PWM2: R7.2, U1.36 (PB15)
RST: C15.1, JP1.10 (!RESET), R3.2, S1.1, S1.2, U1.7 (NRST)
SCK: JP10.2, JP15.2, U1.55 (PB3)
SWCLK: JP1.4 (SWDCLK/TCK), U1.49 (PA14)
SWDIO: JP1.2 (SWDIO/TMS), U1.46 (PA13)
VIN: J1.2, J6.2, U$1.12 (VBAT), U$2.12 (VBAT), U$3.3 (S), U$4.3 (S)
VOUT: C11.+, C12.+, C13.+, U$1.3 (VCC), U$1.13 (VCC), U$1.23 (VCC), U$1.VCC, U$1.VCC@1 (VCC), U$2.3 (VCC), U$2.13 (VCC), U$2.23 (VCC), U$2.VCC, U$2.VCC@1 (VCC), U$3.2 (D), U$4.2 (D)

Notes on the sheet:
Main MCU
Motor Driver
ID SELECTION
2 AMP DUPONT
CAN BUS
POWER SUPPLY


Board: 2 copper layers, 100.0 x 100.0 mm, 69 parts (0 on the bottom side), 63 nets.

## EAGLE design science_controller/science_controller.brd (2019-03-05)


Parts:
C1, C2: 22pF; C0805
C3, C4: 1uF; C0805
C5, C6, C7, C8, C9, C10: 0u1F; C0805
C11: 4u7F; C0805
CON1, CON2: UAVCAN_MICRO; SM04B-GHS-TB
JP1: CORTEX-M-DBG; FTSH-105-01-F-DV-007
R1, R2: 4k7; R0805
U1: STM32F303CB; LQFP48
U2: AP2112K-3.3TRG1; SOT25
U$3: MCP2562-E/SN; SOIC8
Y1: NX5032

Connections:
+3V3: C4.1, C6.1, C7.1, C8.1, C9.1, C10.1, C11.1, JP1.1 (VCC), R1.2, R2.2, U1.9 (VDDA), U1.24 (VDD_1), U1.36 (VDD_2), U1.48 (VDD_3), U2.5 (VOUT), U$3.5 (VIO); also elsewhere on the board
+5V: C3.1, C5.1, CON1.1 (+5V), CON2.1 (+5V), U2.1 (VIN), U2.3 (EN), U$3.3 (VDD); also elsewhere on the board
ACC_DRDY: U1.15 (PA5); also elsewhere on the board
ACC_INT1: U1.16 (PA6); also elsewhere on the board
ACC_INT2: U1.17 (PA7); also elsewhere on the board
CAN_RXD: U1.32 (PA11), U$3.4 (RXD)
CAN_TXD: U1.33 (PA12), U$3.1 (TXD)
GND: C1.2, C2.2, C3.2, C4.2, C5.2, C6.2, C7.2, C8.2, C9.2, C10.2, C11.2, CON1.4 (GND), CON1.TAB_A (TABS), CON1.TAB_B (TABS), CON2.4 (GND), CON2.TAB_A (TABS), CON2.TAB_B (TABS), JP1.3 (GND_1), JP1.5 (GND_2), JP1.9 (GND_DETECT), U1.8 (VSSA/VREF-), U1.23 (VSS_1), U1.35 (VSS_2), U1.47 (VSS_3), U2.2 (GND), U$3.2 (VSS), U$3.8 (STBY); also elsewhere on the board
GPS_XRST: U1.10 (PA0); also elsewhere on the board
GPS_XSTBY: U1.11 (PA1); also elsewhere on the board
unnamed: C1.1, U1.5 (PF0/OSC_IN), Y1.P$2 (2)
unnamed: C2.1, U1.6 (PF1/OSC_OUT), Y1.P$1 (1)
unnamed: CON1.2 (CANH), CON2.2 (CANH), U$3.7 (CANH)
unnamed: CON1.3 (CANL), CON2.3 (CANL), U$3.6 (CANL)
NRST: JP1.10 (!RESET), U1.7 (NRST)
SCL: R1.1, U1.42 (PB6); also elsewhere on the board
SDA: R2.1, U1.43 (PB7); also elsewhere on the board
SWCLK: JP1.4 (SWCLK/TCK), U1.37 (PA14)
SWDIO: JP1.2 (SWDIO/TMS), U1.34 (PA13)
SWO: JP1.6 (SWO/TDO), U1.39 (PB3)
USART1_RX: U1.31 (PA10); also elsewhere on the board
USART1_TX: U1.30 (PA9); also elsewhere on the board
USART2_RX: U1.13 (PA3); also elsewhere on the board
USART2_TX: U1.12 (PA2); also elsewhere on the board

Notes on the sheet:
Alternate Function is for I2C1
Enable pullup resistors!
We need to add I2C multiplexer for CO2 sensors. Adafruit TCA9548A
CAN Bus
3v3 Supply
JTAG Header
MCU Crystal
MCU Power
MCU GPIO
For that we need an I2C output with power and ground
I2C Pullups


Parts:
P1: I2C-PWR; TE_5-103669-3
U$1: COPERN2-DIP
U$2: LSM303-BRKOUT; 1X08

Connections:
+3V3: P1.P$1 (VCC), U$1.12 (VBAT), U$1.18 (VCC); also elsewhere on the board
+5V: U$2.7 (VIN); also elsewhere on the board
ACC_DRDY: U$2.5 (DRDY); also elsewhere on the board
ACC_INT1: U$2.4 (I1); also elsewhere on the board
ACC_INT2: U$2.3 (I2); also elsewhere on the board
GND: P1.P$4 (GND), U$1.19 (GND), U$2.6 (GND); also elsewhere on the board
GPS_XRST: U$1.17 (XRST); also elsewhere on the board
GPS_XSTBY: U$1.20 (XSTBY); also elsewhere on the board
SCL: P1.P$3 (SCL), U$2.1 (SCL); also elsewhere on the board
SDA: P1.P$2 (SDA), U$2.2 (SDA); also elsewhere on the board
USART1_RX: U$1.4 (RX-B); also elsewhere on the board
USART1_TX: U$1.8 (TX-B); also elsewhere on the board
USART2_RX: U$1.5 (RX-A); also elsewhere on the board
USART2_TX: U$1.7 (TX-A); also elsewhere on the board

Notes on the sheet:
GPS
Accelerometer
External I2C Connector


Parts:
J1: ED350/2
JP2, JP3, JP4: PINHD-16; 1X16
U3: PCA9685PW; TSSOP28

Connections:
+5V: U3.28 (VDD); also elsewhere on the board
GND: J1.2, JP4.1, JP4.2, JP4.3, JP4.4, JP4.5, JP4.6, JP4.7, JP4.8, JP4.9, JP4.10, JP4.11, JP4.12, JP4.13, JP4.14, JP4.15, JP4.16, U3.1 (A0), U3.2 (A1), U3.3 (A2), U3.4 (A3), U3.5 (A4), U3.14 (VSS), U3.24 (A5); also elsewhere on the board
SCL: U3.26 (SCL); also elsewhere on the board
SDA: U3.27 (SDA); also elsewhere on the board
SERVO0: JP2.1, U3.6 (LED0)
SERVO1: JP2.2, U3.7 (LED1)
SERVO2: JP2.3, U3.8 (LED2)
SERVO3: JP2.4, U3.9 (LED3)
SERVO4: JP2.5, U3.10 (LED4)
SERVO5: JP2.6, U3.11 (LED5)
SERVO6: JP2.7, U3.12 (LED6)
SERVO7: JP2.8, U3.13 (LED7)
SERVO8: JP2.9, U3.15 (LED8)
SERVO9: JP2.10, U3.16 (LED9)
SERVO10: JP2.11, U3.17 (LED10)
SERVO11: JP2.12, U3.18 (LED11)
SERVO12: JP2.13, U3.19 (LED12)
SERVO13: JP2.14, U3.20 (LED13)
SERVO14: JP2.15, U3.21 (LED14)
SERVO15: JP2.16, U3.22 (LED15)
SERVO_!OE: U3.23 (!OE)
VCC: J1.1, JP3.1, JP3.2, JP3.3, JP3.4, JP3.5, JP3.6, JP3.7, JP3.8, JP3.9, JP3.10, JP3.11, JP3.12, JP3.13, JP3.14, JP3.15, JP3.16

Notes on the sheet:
Standard servo pinout: Signal -> Power -> Ground
Servo Output
Servo Power


Board: 2 copper layers, 100.0 x 100.0 mm, 28 parts (0 on the bottom side), 41 nets.

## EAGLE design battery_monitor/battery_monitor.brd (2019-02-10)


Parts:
C1: 0u1F; C0805
C2, C3, C4: 100n; C0805
C5: 4u7; C0805
C6, C9, C10: 1uF; C0805
C7: 10nF; C0805
C8: 0u1; C0805
C11, C12: 22pF; C0805
CON1, CON2: SM04B-GHS-TB
J1: 2PIN_HDR; 2PIN-HDR
JP1: CORTEX-M-DBG; FTSH-105-01-F-DV-007
LED1, LED2: LEDCHIPLED_0805; CHIPLED_0805
PCON1: WIREPAD_DUAL-10AWG
R1, R7, R8: 1K; R0805
R2, R3, R6, R10: 10K; R0805
R4: 100; R0805
R5: 100K; R0805
R9: 90K; R0805
S1, S2: MOMENTARY-SWITCH-SPST-2-SMD-4.6X2.8MM; TACTILE_SWITCH_SMD_4.6X2.8MM
U1: STM32F303CB; LQFP48
U$1, U$2: IPB120P04P4L03ATMA1; INFINEON_PG-TO263-3-2
U$3: T2N7002AK,LM; SOT23
U$4: 20U_PC_SHUNT; RSENSE_20U
U$5: PP45_HOR_4GRD
U$6: INA145; SOIC8
U$7: MCP2562-E/SN; SOIC8
U$8: RICHTEK_RT9058; SOT23
Y1: NX5032

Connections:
+3V3: C1.2, C2.1, C3.1, C4.1, C5.1, C6.1, C7.1, C9.1, JP1.1 (VCC), R6.2, R7.2, U1.1 (VBAT), U1.9 (VDDA), U1.24 (VDD_1), U1.36 (VDD_2), U1.48 (VDD_3), U$6.7 (V+), U$7.5 (VIO), U$8.2 (VOUT)
+5V: C8.1, CON1.P$1, CON2.P$1, U$7.3 (VDD)
+VBAT: C10.1, PCON1.+, R1.2, R9.1, U$1.P$3 (S1), U$2.P$3 (S1), U$8.1 (VIN)
CANH: CON1.P$2, CON2.P$2, U$7.7 (CANH)
CANL: CON1.P$3, CON2.P$3, U$7.6 (CANL)
CANRX: U1.32 (PA11), U$7.4 (RXD)
CANTX: U1.33 (PA12), U$7.1 (TXD)
GND: C1.1, C2.2, C3.2, C4.2, C5.2, C6.2, C7.2, C8.2, C9.2, C10.2, C11.2, C12.2, CON1.P$4, CON1.P$5, CON1.P$6, CON2.P$4, CON2.P$5, CON2.P$6, JP1.3 (GND_1), JP1.5 (GND_2), JP1.9 (GND_DETECT), LED1.C, LED2.C, PCON1.-, R2.1, R4.2, R10.2, S1.1, S1.2, S2.3, S2.4, U1.8 (VSSA/VREF-), U1.23 (VSS_1), U1.35 (VSS_2), U1.44 (BOOT0), U1.47 (VSS_3), U$3.2 (S), U$5.-_1 (-), U$5.-_2 (-), U$6.1 (REF), U$6.4 (V-), U$7.2 (VSS), U$7.8 (STBY), U$8.3 (GND)
ISENSE_A: U$1.P$2 (D1), U$2.P$2 (D1), U$4.P$1 (1), U$4.P$3 (1), U$6.2 (IN-)
ISENSE_OUT: R5.1, U1.10 (PA0), U$6.6 (OUT)
MCU_OUT_EN: J1.P$1, U1.38 (PA15)
unnamed: R1.1, U$1.P$1 (G1), U$2.P$1 (G1), U$3.3 (D)
unnamed: R3.1, U$6.5 (VG)
unnamed: R3.2, R4.1, R5.2
unnamed: LED1.A, R7.1
unnamed: LED2.A, R8.1
NRST: JP1.10 (!RESET), R6.1, S1.3, S1.4, U1.7 (NRST)
OSC_IN: C11.1, U1.5 (PF0/OSC_IN), Y1.P$2 (2)
OSC_OUT: C12.1, U1.6 (PF1/OSC_OUT), Y1.P$1 (1)
OUT_EN: J1.P$2, R2.2, R8.2, U$3.1 (G)
SWCLK: JP1.4 (SWCLK/TCK), U1.37 (PA14)
SWDIO: JP1.2 (SWDIO/TMS), U1.34 (PA13)
SWO: JP1.6 (SWO/TDO), U1.39 (PB3)
USR_BTN: S2.1, S2.2, U1.11 (PA1)
VBAT_MEASURE: R9.2, R10.1, U1.12 (PA2)
VOUT: U$4.P$2 (2), U$4.P$4 (2), U$5.+_1 (+), U$5.+_2 (+), U$6.3 (IN+)

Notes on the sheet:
MOSFET Control
Current Sense Diff. Amplifier
1% Tolerance Resistors
Datasheet Recommended
MCU Power
CAN Bus
Analog Supply Decoupling
Digital Supply Decoupling
Power Input
Power
Output Enable
Indication
Power Regulation
Programming Header
Isense is ADC1_IN1. Vbat is ADC1_IN3
Capacitor Values should be tweaked. 22pF works but we don't know if it's optimal.
Battery Voltage Divider (1/10)
RT9058


Board: 2 copper layers, 90.0 x 110.0 mm, 41 parts (0 on the bottom side), 26 nets.

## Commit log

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2018-06-27 Add files via upload
    First ver of arm encoder
    [Main.kicad_pcb, Main.sch]
2018-06-29 Made some changes to arm position sensor. - Corrected potentiometer footprint. - Made mounting holes and overall size nice numbers (20x35 and 30x45). - Added some silkscreen features.
    [Main.kicad_pcb]
2018-06-29 Renamed folder from 'SPEAR arm position' to 'SPEAR-arm-position' to follow naming conventions.
    [Main.kicad_pcb, Main.sch]
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2018-07-04 Generated arm position Gerbers
    [Main-B.Cu.gbr, Main-B.Mask.gbr, Main-B.SilkS.gbr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]
2018-08-30 Deleted all the old PCBs and everything.
    [Arm-Controller-B.Cu.gbr, Arm-Controller-B.Mask.gbr, Arm-Controller-B.SilkS.gbr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]
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2018-08-30 Completed can termination schematic
    [can_termination.kicad_pcb, can_termination.sch]
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2018-09-01 ~~stole~~ *borrowed* communication's hub design from ARVP.
    Thanks ARVP!
    [communication-hub.kicad_pcb, communication-hub.sch]
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2018-09-01 Fixed some potential issues with TCAN/MCP parts
    [communication-hub.kicad_pcb]
2018-09-05 Added CAN bus template.
    TODO:
    - Change meta/info.html to be better than it is.
    - Make the template icon fit properly.
    [canbus_basic.kicad_pcb, canbus_basic.sch]
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2018-09-16 made the CAN Bus HAT
    [can bus hat.brd, can bus hat.sch]
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2018-09-16 fixed footprint mcp2562 and modify raspberry pi HAT
    [can bus hat.brd, can bus hat.sch]
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2018-09-21 Added Cree RGB LED and PCA9685 to library.
    [indication.sch]
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2018-09-23 Started drive_pdu tutorial stuff
    [drive_pdu.sch]
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2018-09-28 added step file for arm-controller with minor changes
    [Arm controller.brd, Arm controller.sch]
2018-10-05 Made more progress. Schematic mostly done.
    [indication.sch]
2018-10-06 Changes to PCB Design
    [Arm controller.brd, Arm controller.sch]
2018-10-14 Added St link v2 connection, with some modification of step file
    [Arm controller.brd, Arm controller.sch]
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2018-10-15 Finished schematic, started layout
    [indication.brd, indication.sch]
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2018-10-15 Fixed some footprint issues and most of positioning.
    I botched a few footprints so I had to fix them :/
    [indication.brd, indication.sch]
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2018-10-17 Finished a lot of routing.
    Most of the PCA9685 stuff is routed.
    Todo:
    - Add programming header.
    - Route everything else.
    - Add planes.
    [indication.brd, indication.sch]
2018-10-27 Updated some parts of the library, with changes in added
    [Arm controller.brd, Arm controller.sch]
2018-11-10 Finished Layout.
    - Passes DRC.
    [indication.brd]
2018-11-10 Fixed a few little things I noticed.
    [indication.brd]
2018-11-17 Creaded battery monitor project and BOM
    [BOM.ods]
2018-11-17 Added Infineon PG-TO26-3-2 footprint.
    [BOM.ods]
2018-11-17 Started work on schematic.
    [battery_monitor.sch]
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2018-11-22 Schematic is finished (maybe)
    [BOM.ods, battery_monitor.brd, battery_monitor.sch]
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2018-11-23 Improved Silkscreen and finished dimensioning.
    [battery_monitor.brd]
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2018-11-24 Changed BOM a bit
    [BOM.ods]
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2018-12-04 Updated BOM for out of stock parts
    [BOM.ods]
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2018-12-08 Added update potentiometer board.
    [Main.kicad_pcb, Main.sch]
2018-12-09 Fixed footprint stuff and added 3d model for pot.
    [Main.kicad_pcb]
2018-12-14 Added dimensioning and tweaked dimensions slightly.
    [DrivePDU.brd]
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2019-01-03 Started work on schematic for science controller.
    [science_controller.sch]
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2019-02-01 Updated battery monitor design.
    - Added cortex debug header.
    - Added voltage divider to read voltage from batteries.
    - Added 8MHz crystal oscillator
    [battery_monitor.brd, battery_monitor.sch]
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2019-02-10 Did stuff.
    Still need to add bypass caps, CAN bus stuff,
    and possibly an I2C multiplexer.
    [science_controller.sch]
2019-02-11 Nearly done the schematic.
    Unless I'm wrong, all that's left is I2C output.
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2019-03-05 Finished first revision of science controller board.
    Needs review!
    [Bom.csv, science_controller.brd, science_controller.sch]
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2019-03-09 Moved arm controller BOM to correct place
    [Bom.csv]
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2019-03-23 changes based on last pull request enter the commit message for your changes. Lines starting
    [Arm controller Mega.brd, Arm controller Mega.sch]
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2019-05-04 Fixed some things
    [DriveControllerBoard.brd, DriveControllerBoard.sch]
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2019-07-03 Fixing errors. Still a few to be fixed.
    [DriveControllerBoard.brd, DriveControllerBoard.sch]
2019-07-03 corrected layout issues.
    [DriveControllerBoard.brd]
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2019-07-10 fixed issues with board not being in sync with schematic
    [ARM_PDU.brd, ARM_PDU.sch]
2019-07-10 fixed hole size issues
    [ARM_PDU.brd, ARM_PDU.sch]
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2019-10-19 uploaded bom, PnP, and change some board layout:
    [BOM.xlsx, Green Pill Sparkfun.brd, Green Pill Sparkfun.sch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]
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2019-10-21 fixed error in PnP file
    [PnP file.xlsx]
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2019-11-21 fixed wire stub, changes based on request
    [arm controller single.brd, arm controller single.sch]
2019-11-21 fixed silkscreen
    [arm controller single.brd]
2019-11-22 fixed DRC
    [arm controller single.brd, arm controller single.sch]
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2020-03-01 Changed the indication board so it uses higher power LED's now
    [indication.brd, indication.sch]
2020-03-10 fixed hole size for speedy footprint
2020-03-11 updated to new relay to commonly used songle 10A, minor changes to layout.
    [Comp PDU.brd, Comp PDU.sch]
2020-03-17 Moved some silkscreen so they weren't on top of eachother
    [indication.brd]
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2020-03-19 add connectors for battery monitoring, add more protection to ADC Lines
    [Comp PDU.brd, Comp PDU.sch]
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2020-04-05 fixed schematic, started board
    [sub_sys_pdu.brd, sub_sys_pdu.sch]
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2020-04-05 renamed vias to GND and fixed drill size
    [sub_sys_pdu.brd]
2020-04-08 fixed some issues and put board name and author on board
    [sub_sys_pdu.brd]
2020-04-09 Fixed everything that needed to be fixed (hopefully)
    [indication.brd, indication.sch]
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2020-04-26 made the board a bit smaller and other small changes
    [DriveControllerBoard.brd, DriveControllerBoard.sch]
2020-05-06 increased size of power traces and some other traces
    [indication.brd]
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2020-05-13 Added magnetic encoder design as as5600-encoder
    [Work done by minh]
    [as5600_adapter.brd, as5600_adapter.sch]
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2020-06-05 Fixed traces, added BOM
    [Bom_8263902.xlsx, IMU.brd, IMU.sch]
2020-06-06 Fixing bom
    [Bom_8263902.xlsx]
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2023-06-30 speedy-breakout: Add headers for feedback expansion
    This consists of a footprint for an arbitrary 2.54 mm connector, with
    traces to another header which can be used to easily solder wires to
    make arbitrary connections to the Speedy breakout through-holes
    depending on the desired application. A 6 pin footprint was used which
    should give enough for power + ground and up to a full 4 pin SPI
    interface. Pin 6 is tied to ground.
    [speedy-breakout.kicad_pcb, speedy-breakout.kicad_sch]
2023-10-29 speedy-breakout: Add generated outputs
    This adds the generated gerber outputs, 3D CAD models,
    and schematic PDF for quick reference and use.
    [speedy-breakout-B_Cu.gbl, speedy-breakout-B_Mask.gbs, speedy-breakout-B_Paste.gbp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]
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2023-11-19 Remove unnecessary files in repository root
    There were some arm controller related files in the root of the project
    directory which are not needed.
    [bom_single.xlsx]
2023-11-26 eagle: Remove Inertial_measurement_unit
    We no longer use eagle and anything here that we need should have
    already been imported into KiCad. This commit can easily be reverted
    if we need this project.
    [Bom_8267665.xlsx, IMU.brd, IMU.sch]
2023-11-26 eagle: Remove arm-controller-stm32f303cct6
    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
    [arm controller single v1.1.brd, arm controller single v1.1.sch, arm controller single.brd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]
2023-11-26 eagle: Remove as5600-encoder
    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
    [as5600_adapter.brd, as5600_adapter.sch]
2023-11-26 eagle: Remove communication-hub
    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
    [communication-hub.brd, communication-hub.sch]
2023-11-26 eagle: Remove comp-pdu
    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
    [Comp PDU.brd, Comp PDU.sch, boost module.brd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]
2023-11-26 eagle: Remove spear-dev-board
    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
    [BOM.xlsx, Green Pill stlink.brd, Green Pill stlink.sch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]
2023-11-26 eagle: Remove sub_sys_pdu
    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
    [sub_sys_pdu.brd, sub_sys_pdu.sch]
2023-11-26 eagle: Remove eagle_libs
    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
2023-11-26 archive: Remove arm-controller
    Git preserves the history of the repo so there isn't any need to keep
    old projects around. This commit can easily be reverted if we need to
    move it out of the archive.
    [Arm controller Mega.brd, Arm controller Mega.sch, Arm controller.brd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]
2023-11-26 archive: Remove arm_pdu
    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
    [ARM_PDU.brd, ARM_PDU.sch]
2023-11-26 archive: Remove battery_monitor
    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
    [BOM.ods, battery_monitor.brd, battery_monitor.sch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]
2023-11-26 archive: Remove can_indication
    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
    [BOM.ods, indication.brd, indication.sch]
2023-11-26 archive: Remove can_termination
    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
    [can_termination.kicad_pcb, can_termination.sch]
2023-11-26 archive: Remove drive_controller
    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
    [DriveControllerBoard.brd, DriveControllerBoard.sch]
2023-11-26 archive: Remove drive_pdu
    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
    [BOM.csv, DrivePDU.brd, DrivePDU.sch]
2023-11-26 archive: Remove main-pdu
    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
    [Main PDU.brd, Main PDU.sch]
2023-11-26 archive: Remove science_controller
    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
    [science_controller.brd, science_controller.sch]

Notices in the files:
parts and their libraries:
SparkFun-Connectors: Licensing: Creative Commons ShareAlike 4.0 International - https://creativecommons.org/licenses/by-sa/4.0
